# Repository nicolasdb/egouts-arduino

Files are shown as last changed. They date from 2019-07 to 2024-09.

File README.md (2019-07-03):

# MUSEE DES EGOUTS
Une maquette sur le cycle anthropique de l’eau et de supports didactiques  
Projet Arduino pour l'automatisation des écoulements d'eau.   

## Appel à projet remporté par:

**Ignacio Plaza De Giles** : architecte, maquettiste  
_Conception et réalisation + modelisation 3D, impression 3D, découpe laser_  
**Nicolas de Barquin** : co-fondateur de OpenFab  
_Conception et réalisation + support technique sur le design et l’électronique_  
**Juan Vandeput** : menuisier, ébéniste  
_Conception et réalisation + construction bois_  
**Alexandra Sebbag** : graphiste  
_Conception et réalisation des jeux + design et légendes de la maquette_  
**Hélène Mariage** : paysagiste, maquettiste  
_Conception et réalisation + communication, logistique_  

blob

## Storm simulation

arduino Board - LEDs orage



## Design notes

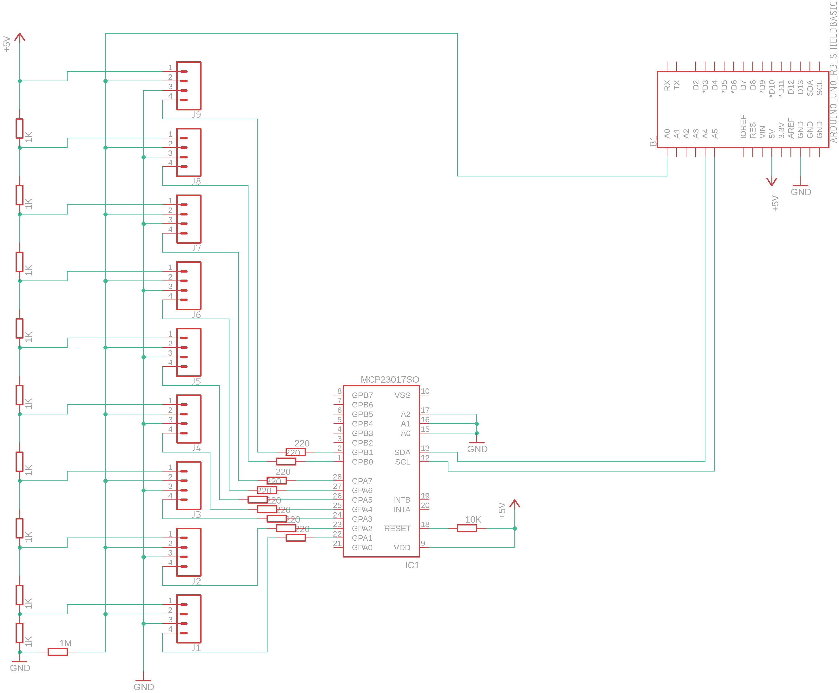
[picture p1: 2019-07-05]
ArduinoShield/schéma boutons.png

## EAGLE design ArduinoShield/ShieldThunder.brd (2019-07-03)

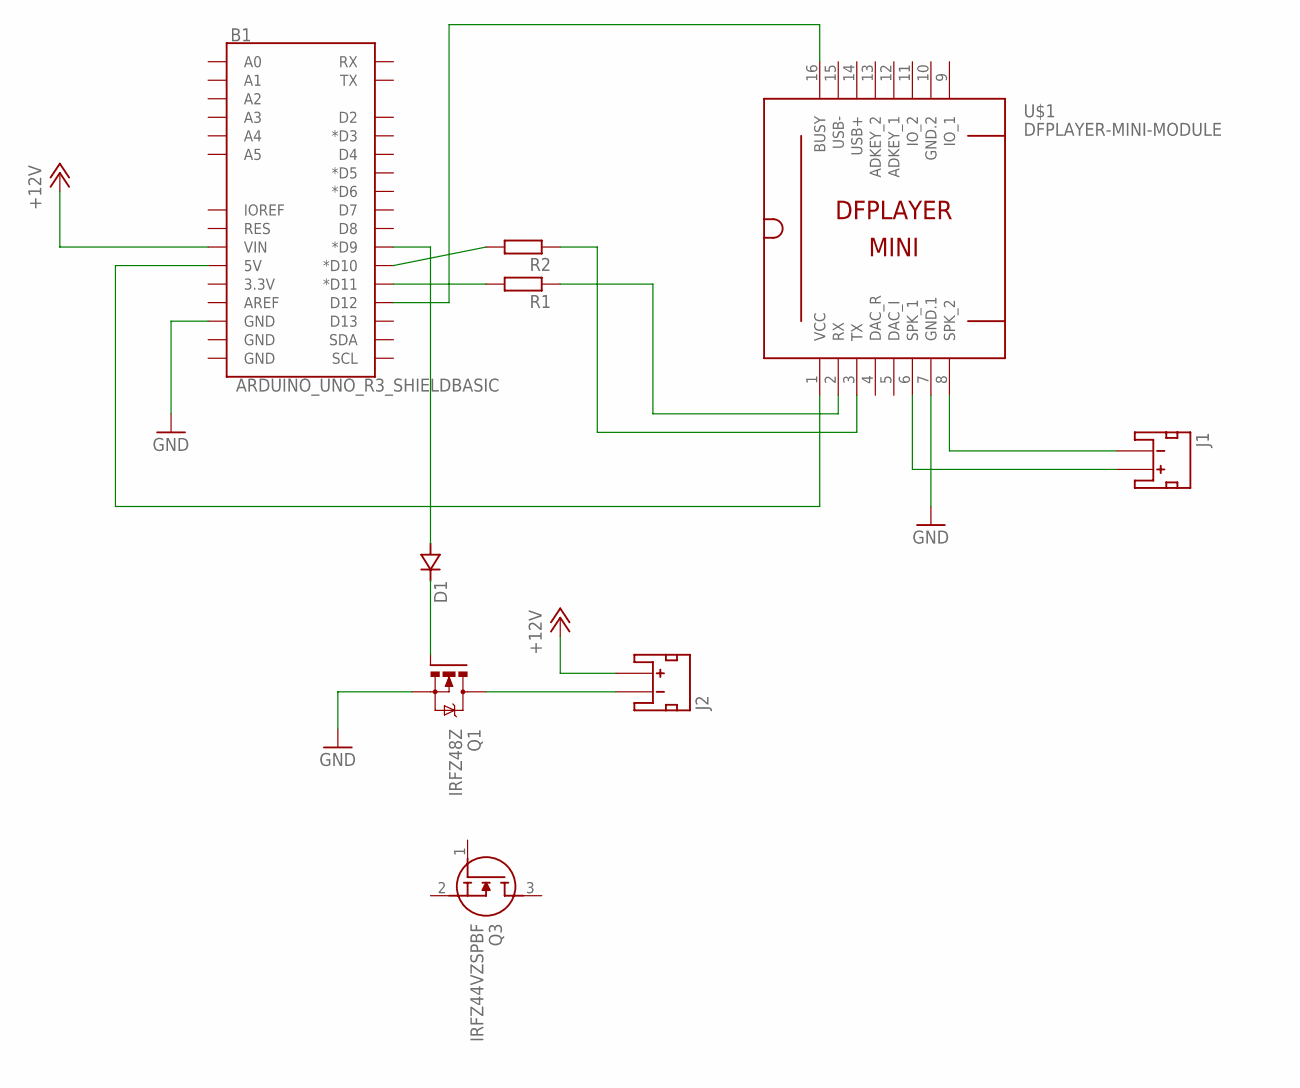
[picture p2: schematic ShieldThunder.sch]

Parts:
B1: ARDUINO_UNO_R3_SHIELDBASIC; UNO_R3_SHIELD
D1: DSOT23; SOT-23
J1, J2: JST_2MM_MALE; JST-2-SMD
Q1: IRFZ48Z; TO220BH
Q3: IRFZ44VZSPBF; D2PAK(TO-263AB)
R1, R2: R-EU_R0805; R0805
U$1: DFPLAYER-MINI-MODULE

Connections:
+12V: B1.VIN, J2.2 (+)
GND: B1.GND@2 (GND), Q1.S, U$1.7 (GND.1)
GND.2: U$1.10 (GND.2)
unnamed: B1.D10 (*D10), R2.2
unnamed: B1.D11 (*D11), R1.2
unnamed: R1.1, U$1.2 (RX)
unnamed: R2.1, U$1.3 (TX)
unnamed: B1.D12, U$1.16 (BUSY)
unnamed: J1.2 (+), U$1.6 (SPK_1)
unnamed: J1.1 (-), U$1.8 (SPK_2)
unnamed: B1.D9 (*D9), D1.3 (A)
unnamed: D1.1 (C), Q1.G
unnamed: J2.1 (-), Q1.D
unnamed: B1.5V, U$1.1 (VCC)

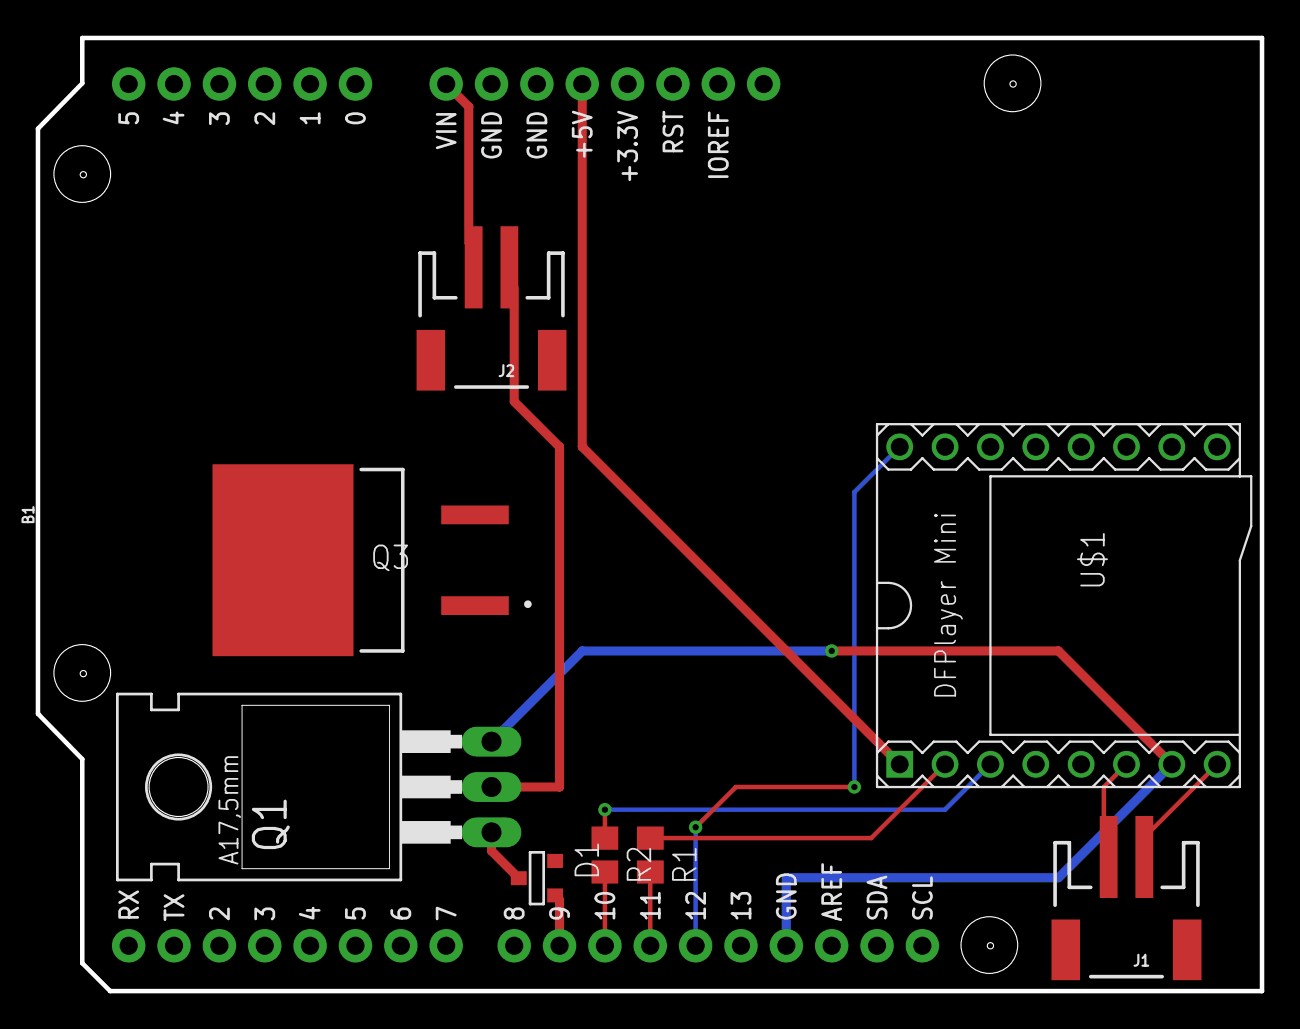
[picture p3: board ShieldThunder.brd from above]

Board: 2 copper layers, 68.5 x 53.4 mm, 9 parts (0 on the bottom side), 13 nets.

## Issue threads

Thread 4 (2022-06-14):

DFplayer mini setup

nicolasdb, 2022-06-14:
J'ai toujours des problèmes de son.
J'ai testé le module seul avec une activation par push button, ça fonctionne.
Et les bugs apparaissent avec la connexion à Arduino.
Je teste avec la proposition de [claudiusmarius](https://github.com/claudiusmarius)
https://github.com/claudiusmarius/Double-Player-Avec-ATtiny84

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

nicolasdb, 2022-06-14:
mes tests se font avec un petit HP 8ohm, mais l'installation finale est équipée de 2x 4ohm. ça a marché pendant 2 ans, sauf que ça ne marche pas à l'atelier sur un seul 4ohm similaire....

je vais tester d'en brancher 2

nicolasdb, 2022-06-14:
Problème aussi de surchauffe.
Le module chauffe rapidement, peut-être que l'ajout de la diode zener et les condo aidera.... à suivre.

nicolasdb, 2022-06-14:
Good,
les ajouts de Condensateurs et diode zener maintienne le module frais.
Mais j'ai encore eu des soucis de connection après la mise sous tension, un reset était nécessaire 1x.... que j'ai résolu pour l'instant en rajoutant un `delay(1000);` avant le chargement de la librairie mp3.
Juste de quoi laisser le temps au système de se stabiliser après mise sous tension. Peut-être les condensateurs.

J'ai encore un doute sur les HP.
celui de test en 8ohm fonctionne.

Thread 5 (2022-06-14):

détection série multiples Boutons d'arcade - instabilité

nicolasdb, 2022-06-14:
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

Le problème initial était le manque de PIN sur arduino, problème solutionné ensuite par l'ajout de multiplexer MCP23017.
Je pourrais renvoyer la détection INPUT des boutons sur le MCP0, mais je devrai alors revoir le code.
Ce qui n'est pas prévu dans cette révision.
J'ai 5 boutons poussoir monté en série, inspiré de ceci:

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
https://rayshobby.net/wordpress/multiple-button-inputs-using-arduino-analog-pin/

Mais j'observe une instabilité dans le système.
- Lorsque je branche l'alimentation, un bouton est automatiquement déclenché.
peut-être ajouter un condo, il doit y avoir une surtension qui acte comme un bouton... lequel?
- En fonction que j'alimente par transfo 9V, 12V sur l'arduino. Ou encore que j'ai l'USB connecté ou pas, lorsque je veux prendre mes mesures via le monitor,
la tension en sortie 5V est légèrement modifiée et ça fait varier la mesure sur le pin A0 (A3 dans mon code)
Et la mesure change au point que l'assignation des boutons changent. Les plages d'identification sont pourtant assez large...

```
for (;;) {

    if (etats == IDLE) {
      int buttonValue=analogRead(A3);
      Serial.print("Waiting entry");
      Serial.println(buttonValue);
      if (buttonValue>751) {                                         // read: 1013
        Serial.println("Button 1");
        buttonID = 1;
        etats = S1;
      } else if (buttonValue >= 726 && buttonValue < 925) {          // read: 815
        Serial.println("Button 2");
        buttonID = 2;
        // etats = IDLE;
        etats = S2;
      } else if (buttonValue >= 501 && buttonValue < 725) {          // read: 614
        Serial.println("Button 3");
        buttonID = 3;
        // etats = IDLE;
        etats = S3;
      } else if (buttonValue >= 251 && buttonValue < 500) {          // read: 409
        Serial.println("Button 4");
        buttonID = 4;
        // etats = IDLE;
        etats = S4;
      } else if (buttonValue >= 101 && buttonValue < 250) {          // read: 214
        Serial.println("Button 5");
        buttonID = 5;
        // etats = IDLE;
        etats = S5;
      }
    }
    vTaskDelay(1);
  }
```

nicolasdb, 2022-06-14:
ok, dans le cas précédent les R1K s'additionnaient. D'où peut-être trop d'instabilité dans les valeurs.

Je testerai selon cette proposition:
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

> We connect a single 100K resistor between GND and the analog input, with the analog input also connected to one leg of all of the push buttons. We then connect different resistors between the 5V and the second leg of each of the push buttons. It is important that each of these resistors are different values so that you get different voltages on the analog input, enabling you to identify each button.
https://www.the-diy-life.com/multiple-push-buttons-on-one-arduino-input/

nicolasdb, 2022-06-14:
Mise à jour:
- remplacement des résistances pour mode //
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
- et ajout d'un "debounce" software
```
void TaskButtons(void *pvParameters)
{
  (void) pvParameters;

  for (;;) {

    if (etats == IDLE) {
      int buttonValue=analogRead(A3);
      delay(20);
      int buttonValue2=analogRead(A3);
      Serial.print("Waiting entry");
      Serial.println(buttonValue);
      if (buttonValue >= 950 && buttonValue2 >= 950){                                      // 10R read: 1021
        Serial.println("Button 1");
        buttonID = 1;
        // etats = IDLE;
        etats = S1;
      } else if (buttonValue >= 876 && buttonValue < 949 && buttonValue2 >= 876 && buttonValue2 < 949) {          // 10K read: 930
        Serial.println("Button 2");
        buttonID = 2;
        // etats = IDLE;
        etats = S2;
      } else if (buttonValue >= 751 && buttonValue < 875 && buttonValue2 >= 751 && buttonValue2 < 875) {          // 22K read: 840
        Serial.println("Button 3");
        buttonID = 3;
        // etats = IDLE;
        etats = S3;
      } else if (buttonValue >= 351 && buttonValue < 750 && buttonValue2 >= 351 && buttonValue2 < 750) {          // 56K read: 659
        Serial.println("Button 4");
        buttonID = 4;
        // etats = IDLE;
        etats = S4;
      } else if (buttonValue >= 150 && buttonValue < 350 && buttonValue2 >= 150 && buttonValue2 < 350) {          // 210K read: 280
        Serial.println("Button 5");
        buttonID = 5;
        // etats = IDLE;
        etats = S5;
      }
    }
    vTaskDelay(1);
  }
}
```

ça à l'air pas mal.

Closed 2023-03-04.

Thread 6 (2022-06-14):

Activation des 16 relais

nicolasdb, 2022-06-14:
https://www.utmel.com/components/bc337-npn-transistor-pinout-datasheet-and-equivalents?id=347

nicolasdb, 2022-06-14:
J11 et J13 sont les pin 5V et GND que j'ai externalisé du header 10pin pour choisir entre une alimentation provenant de la carte controle ou via une alim externe sur les connecteurs en bas à droite du module.

nicolasdb, 2022-06-14:
Note pour une upgrade.
Est-ce que ULN2803 pourrait remplacer les transistors BC337

https://pijaeducation.com/arduino/relay/interfacing-of-relay-with-arduino-using-uln2003/

nicolasdb, 2022-06-18:
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

nicolasdb, 2022-06-18:
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

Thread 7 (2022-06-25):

Boite de simulation

nicolasdb, 2022-06-25:
En attendant que les PCB arrivent, je fabrique une boite de simulation pour tester la programmation sans la maquette.

à quoi sert le 3ème pin des connecteurs 5.5x2.1mm? (barrel power plugs)
https://electronics.stackexchange.com/questions/90529/what-to-do-with-third-contact-in-dc-barrel-plug-with-only-two-input-contacts

nicolasdb, 2022-06-25:
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

à quoi sert le 3ème pin des connecteurs 5.5x2.1mm? (barrel power plugs)
https://electronics.stackexchange.com/questions/90529/what-to-do-with-third-contact-in-dc-barrel-plug-with-only-two-input-contacts

nicolasdb, 2022-07-01:
Pour remplacer les 2 sorties leds-array en 12V, je place 2 leds 9V 402 de chez electron discount

https://www.befr.ebay.be/itm/140668935540

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

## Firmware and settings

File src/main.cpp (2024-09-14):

#include <Arduino.h>
#include <Arduino_FreeRTOS.h>         // Multitasking. Attention version 10.1.1-1!!
#include <SoftwareSerial.h>           // controle du module mp3
#include <DFRobotDFPlayerMini.h>      // controle du module mp3
#include <Wire.h>                     // controle des MCP
#include <Adafruit_MCP23X17.h>        // controle des MCP

#include <mp3.h>                      // controle storm du module mp3 - local

#define portCHAR char                 // resolve error: expected primary-expression before 'const'

// define tasks for Demo, AnalogRead buttons, set Actions, MP3 launch
void TaskDemo( void *pvParameters );          // define demo
TaskHandle_t xDemoHandle = NULL;              // nécessaire pour activer la pause et reprise de la tâche
void TaskButtons( void *pvParameters );       // define Buttons, pour l'écoute de quel bouton est activé
void TaskActions( void *pvParameters );       // define la tâche d'actions.
void TaskPump( void *pvParameters );

// define différent scénario = les actions déclenchées par les boutons lorsque pressé.
enum {
  IDLE,
  S1,S2,S3,S4,S5,S6,S7,S8
} etats;
int buttonID = 0;



// define MCP0 - registre pour les leds bouttons "scénario"
Adafruit_MCP23X17 mcp0;
// define MCP1 - registre pour les electrovannes via relais et options
Adafruit_MCP23X17 mcp1;

int ledButtonArray[] = {7,6,9,8,11,10,5,4};   // liste les pin utilisées sur mcp0 et leur ordre
int count = 0;                                // compteur pour scanner led k2000
int speed = 20;                               // delay pour scanner led k2000



// define n° relay for valves on MCP0 | n°relai>>n°valve
int pump = 0;         //pompe 220V
int ledCiterne = 1;   //citerne 5V
int sterput = 2;     //valve 1-- sterput maison
int citerne = 3;      //valve 2 citerne
int tImper = 4;       //valve 3 pluie toiture G
int tPlant = 5;       //valve 4 pluie toiture D
int egout = 6;       //valve 5 egout champignon
int bOrage = 7;      //valve 6 bassin d'orage
int ledBO2 = 8;       //bassin d'orage bas 5V
int ledBO1 = 9;       //bassin d'orage haut 5V
int pChamp = 10;       //valve 7 pluie champ
int pJardin = 11;      //valve 8 pluie jardin
int collecteur = 12;  //valve 9  collecteur maison (oeuf)
int ruePlace = 13;     //valve 10 rue et place
int riviere = 14;     //valve 11 rivière
int simVille = 15 ;   //valve 12 Maison voisine dans oeuf

// mapping leds
int nappe = 8;          // nappe Phréatique 12V _ Out2
int egg = 7;            // collecteur oeuf 12V - Out1
int sdb1 = 6;
int toilette = 2;
int cuisine = 5;
int arrosage = 4;
int lavelinge = 1;
int cave = 3;

/*--------------------------------------------------*/
/*---------------------- setup ---------------------*/
/*--------------------------------------------------*/
// setup function runs once when you press reset or power the board

void setup() {
  mp3setup();    // initialize mp3setup
  // Serial.begin(115200);

  // INPUT sensors
  pinMode(A3, INPUT);     // input pin buttons scénario

  for (size_t i = 2; i < 9 ; i++){
    pinMode(i, OUTPUT);
    digitalWrite(i,LOW);
    delay(10);
  }
// digitalWrite(2,HIGH);

  // MCP0, define all buttons
  mcp0.begin_I2C(0);                               // use default address 0
  for (size_t i = 0; i < 8 ; i++){
    mcp0.pinMode(ledButtonArray[i], OUTPUT);
    delay(50);
  }

  mcp1.begin_I2C(1);                               // use default address 1
  for (int j = 0; j < 16 ; j++){
    mcp1.pinMode(j, OUTPUT);
    mcp1.digitalWrite(j, LOW);
    delay(50);
  }

  // Serial.println("j'ai finis");
  etats = IDLE;

  // and at last,
  // set up tasks to run independently and their priority.
  xTaskCreate(
    TaskDemo
    ,  (const portCHAR *)"Demo"       // A name just for humans
    ,  128                            // This stack size can be checked & adjusted
                                      // by reading the Stack Highwater
    ,  NULL
    ,  1                              // Priority, with 3 (configMAX_PRIORITIES - 1) being the highest, and 0 being the lowest.
    ,  &xDemoHandle );

  xTaskCreate(
    TaskButtons
    ,  (const portCHAR *)"Buttons"    // A name just for humans
    ,  128                            // This stack size can be checked & adjusted
                                      // by reading the Stack Highwater
    ,  NULL
    ,  3                              // Priority, with 3 (configMAX_PRIORITIES - 1) being the highest, and 0 being the lowest.
    ,  NULL );

  xTaskCreate(
    TaskActions
    ,  (const portCHAR *)"Actions"    // A name just for humans
    ,  128                            // This stack size can be checked & adjusted by reading the Stack Highwater
    ,  NULL
    ,  2                              // Priority, with 3 (configMAX_PRIORITIES - 1) being the highest, and 0 being the lowest.
    ,  NULL );

}

/*--------------------------------------------------*/
/*---------------------- loop ----------------------*/
/*--------------------------------------------------*/
// the loop function is not use here, instead we use FreeRTOS's tasks
void loop()
{
}

/*------------------------------------------------------*/
/*---------------------- functions ---------------------*/
/*------------------------------------------------------*/

// this function will suspend Demo and turn off all led buttons
void suspendDemo () {
  vTaskSuspend(xDemoHandle);
  for (size_t i = 0 ; i < 8 ; i++){
    mcp0.digitalWrite(ledButtonArray[i], LOW);
    vTaskDelay(1);
    }
}

/*--------------------------------------------------*/
/*---------------------- Tasks ---------------------*/
/*--------------------------------------------------*/

/*---------------------- demo ---------------------*/
void TaskDemo(void *pvParameters)  // This is a task.
{
  (void) pvParameters;
  for (;;) {    // on joue la démo en loop : effet scanner k2000
    for (count = 2; count < 6 ; count++){
      mcp0.digitalWrite(ledButtonArray[count], HIGH);
      vTaskDelay(speed / portTICK_PERIOD_MS);
      mcp0.digitalWrite(ledButtonArray[count+1], HIGH);
      vTaskDelay(speed / portTICK_PERIOD_MS);
      mcp0.digitalWrite(ledButtonArray[count], LOW);
      vTaskDelay((speed*5) / portTICK_PERIOD_MS);
    }
    // vTaskDelay( 500 / portTICK_PERIOD_MS ); // wait for one second
    for (count = 6 ; count > 2 ; count--){
      mcp0.digitalWrite(ledButtonArray[count], HIGH);
      vTaskDelay(speed / portTICK_PERIOD_MS);
      mcp0.digitalWrite(ledButtonArray[count-1], HIGH);
      vTaskDelay(speed / portTICK_PERIOD_MS);
      mcp0.digitalWrite(ledButtonArray[count], LOW);
      vTaskDelay((speed*5) / portTICK_PERIOD_MS);
    }
  }
}


/*---------------------- buttons ---------------------*/
void TaskButtons(void *pvParameters)
{
  (void) pvParameters;

  for (;;) {

    if (etats == IDLE) {
      int buttonValue=analogRead(A3);
      // Serial.print("Waiting entry");
      // Serial.println(buttonValue);
      if (buttonValue>810) {
        // Serial.println("Button 8");
        buttonID = ledButtonArray[8-1];
        etats = IDLE;
      } else if (buttonValue > 700 && buttonValue < 809) {
        // Serial.println("Button 7");
        buttonID = ledButtonArray[7-1];
        etats = S5;
      } else if (buttonValue > 610 && buttonValue < 699) {
        // Serial.println("Button 6");
        buttonID = ledButtonArray[6-1];
        etats = S4;
      } else if (buttonValue > 500 && buttonValue < 609) {
        // Serial.println("Button 5");
        buttonID = ledButtonArray[5-1];
        etats = S3;
      } else if (buttonValue > 370 && buttonValue < 499) {
        // Serial.println("Button 4");
        buttonID = ledButtonArray[4-1];
        etats = S2;
      } else if (buttonValue > 270 && buttonValue < 369) {
        // Serial.println("Button 3");
        buttonID = ledButtonArray[3-1];
        etats = S1;
      } else if (buttonValue > 190 && buttonValue <269) {
        // Serial.println("Button 2");
        buttonID = ledButtonArray[2-1];
        etats = IDLE;
      } else if (buttonValue > 90 && buttonValue < 189) {
        // Serial.println("Button 1");
        buttonID = ledButtonArray[1-1];
        etats = IDLE;
      }
    }
    vTaskDelay(1);
  }
}

/*---------------------- actions ---------------------*/
void TaskActions(void *pvParameters)  // This is a task.
{
  for(;;) {
    switch (etats)
    {
    case IDLE:
      buttonID = 0;
      etats = IDLE;
      vTaskResume(xDemoHandle);
      break;


    case S1:              /*---------------------- case Pluie ---------------------*/
      suspendDemo();
      mcp0.digitalWrite(buttonID, HIGH);
        vTaskDelay( 1000 / portTICK_PERIOD_MS );    // wait for 1/2 second
// start scénario
      // eau de pluie, alimentation de la nappe Phréatique
      mcp1.digitalWrite(pump, HIGH);      // start pompe
        piste4(); // activation audio pluie 24'

      mcp1.digitalWrite(pChamp, HIGH);    // start pluie sur
      mcp1.digitalWrite(pJardin, HIGH);   // les surfaces perméables
        vTaskDelay( (1000 / portTICK_PERIOD_MS) * 15 );
      // Waiting x second
      digitalWrite(nappe, HIGH);          // turn on led nappe Phréatique
        vTaskDelay( (1000 / portTICK_PERIOD_MS) * 10 );
      mcp1.digitalWrite(pChamp, LOW);     // stop pluie
      mcp1.digitalWrite(pJardin, LOW);
      mcp1.digitalWrite(pump, LOW);       // stop pompe
        vTaskDelay( (1000 / portTICK_PERIOD_MS) * 3 );
      // on attend un peu pour l'histoire de la nappe Phréatique
      digitalWrite(nappe, LOW);           // turn off led nappe
        vTaskDelay( (1000 / portTICK_PERIOD_MS) * 1 );

// end scénario
      mcp0.digitalWrite(buttonID, LOW);
      etats = IDLE;
      break;

    case S2:              /*---------------------- case Eau potable ---------------------*/
      suspendDemo();
      mcp0.digitalWrite(buttonID, HIGH);
        vTaskDelay( 1000 / portTICK_PERIOD_MS ); // wait for 1/2 second
// start scénario
        // captation eau potable
        digitalWrite(nappe, HIGH);      // turn on nappe Phréatique
          vTaskDelay( (1000 / portTICK_PERIOD_MS) * 10 );
        // on pompe dans la nappe, ou dans la rivière
        digitalWrite(nappe, LOW);
          vTaskDelay( (1000 / portTICK_PERIOD_MS) * 1 );
          // Waiting pompage, chateau d'eau
        digitalWrite(cuisine, HIGH);  // turn on led cuisine
        piste3(); // piste audio robinet 20'
          vTaskDelay( (1000 / portTICK_PERIOD_MS) * 2 );
        //waiting vaisselle, ambiance cuisine
        // turn on pompe et activation du sterput, + led Cave.
        mcp1.digitalWrite(pump, HIGH);
          vTaskDelay( (1000 / portTICK_PERIOD_MS) * .5 );
        // waiting action robinet en cuisine
        // puis turn on sterput à la cave + led
        mcp1.digitalWrite(sterput, HIGH);
        digitalWrite(cave, HIGH);
          vTaskDelay( (1000 / portTICK_PERIOD_MS) * 3 );
        // Waiting trajet de l'eau jusqu'au collecteur rue
        mcp1.digitalWrite(collecteur, HIGH);
        digitalWrite(egg, HIGH);
          vTaskDelay( (1000 / portTICK_PERIOD_MS) * 10 );
          // Waiting end audio robinet
        digitalWrite(cuisine, LOW); // turn of led cuisine
          // Waiting et turn off sertup et led cave
          vTaskDelay( (1000 / portTICK_PERIOD_MS) * 2 );
        mcp1.digitalWrite(sterput, LOW);
        digitalWrite(cave, LOW);
          vTaskDelay( (1000 / portTICK_PERIOD_MS) * 2 );
        mcp1.digitalWrite(collecteur, LOW);
        digitalWrite(egg, LOW);
        mcp1.digitalWrite(pump, LOW);
          vTaskDelay( (1000 / portTICK_PERIOD_MS) * .5 );

// end scénario
      mcp0.digitalWrite(buttonID, LOW);
      // vTaskDelay( (1000 / portTICK_PERIOD_MS) * .5 );
      etats = IDLE;
    break;

    case S3:              /*---------------------- case Épuration ---------------------*/
      suspendDemo();
      mcp0.digitalWrite(buttonID, HIGH);
        vTaskDelay( 1000 / portTICK_PERIOD_MS ); // wait for 1/2 second
// start scénario

digitalWrite(sdb1, HIGH); // turn on sdb
piste5();  //piste audio douche 24'
  vTaskDelay( (1000 / portTICK_PERIOD_MS) * 5 );
  //wait douche, ajout des autres pièces d'eau.
mcp1.digitalWrite(pump, HIGH);  // turn on pompe
    vTaskDelay( (1000 / portTICK_PERIOD_MS) * .5 );
mcp1.digitalWrite(sterput, HIGH);
digitalWrite(cave, HIGH);
  // eau dans la chambre de visite
  vTaskDelay( (1000 / portTICK_PERIOD_MS) * 1 );
  digitalWrite(cuisine, HIGH);
digitalWrite(lavelinge, HIGH); // turn on lavelinge

  vTaskDelay( (1000 / portTICK_PERIOD_MS) * 4 );

  //waiting fin des actions maisons
  vTaskDelay( (1000 / portTICK_PERIOD_MS) * 2 );
  //waiting, l'eau arrive au collecteur rue (egg)
mcp1.digitalWrite(collecteur, HIGH);   //collecteur oeuf + led
digitalWrite(egg, HIGH);
digitalWrite(sdb1, LOW);
  vTaskDelay( (1000 / portTICK_PERIOD_MS) * 1 );
digitalWrite(lavelinge, LOW);
digitalWrite(cuisine, LOW);
  vTaskDelay( (1000 / portTICK_PERIOD_MS) * 2 );
  mcp1.digitalWrite(sterput, LOW);
  digitalWrite(cave, LOW);
mcp1.digitalWrite(bOrage, HIGH);  // l'eau monte un peu
  vTaskDelay( (1000 / portTICK_PERIOD_MS) * 2 );
  //waiting, l'eau arrive au champignon
mcp1.digitalWrite(bOrage, LOW);  // on arrête l'eau au bassin
  vTaskDelay( (1000 / portTICK_PERIOD_MS) * 15 );
  //waiting, l'eau transit jusqu'à la station d'épuration.
mcp1.digitalWrite(riviere, HIGH);
  vTaskDelay( (1000 / portTICK_PERIOD_MS) * 15 );
  mcp1.digitalWrite(collecteur, LOW);   //collecteur oeuf + led
  digitalWrite(egg, LOW);
  //waiting, eau à la rivière
mcp1.digitalWrite(riviere, LOW);
mcp1.digitalWrite(pump, LOW);

// end scénario
      mcp0.digitalWrite(buttonID, LOW);
      etats = IDLE;
    break;

    case S4:              /*---------------------- case Orage ---------------------*/
      suspendDemo();
      mcp0.digitalWrite(buttonID, HIGH);
        vTaskDelay( 1000 / portTICK_PERIOD_MS ); // wait for 1/2 second
// start scénario
        storm(1); // start Orage
        piste4(); // start audio pluie 24'
        mcp1.digitalWrite(pump, HIGH);  // turn on pompe
            vTaskDelay( (1000 / portTICK_PERIOD_MS) * .5 );
        mcp1.digitalWrite(tImper, HIGH);      // pluie toitures maison
        mcp1.digitalWrite(tPlant, HIGH);
        mcp1.digitalWrite(pJardin, HIGH);
        mcp1.digitalWrite(pChamp, HIGH);
          vTaskDelay( (1000 / portTICK_PERIOD_MS) * 10 );
          // Waiting, il pleut
        mcp1.digitalWrite(ruePlace, HIGH);    // eau sur rue&place
          vTaskDelay( (1000 / portTICK_PERIOD_MS) * 5 );
          // Waiting, l'eau coule sur la rue et la place
        mcp1.digitalWrite(tImper, LOW);     // turn off pluie
        mcp1.digitalWrite(tPlant, LOW);
        mcp1.digitalWrite(pJardin, LOW);
        mcp1.digitalWrite(pChamp, LOW);
          vTaskDelay( (1000 / portTICK_PERIOD_MS) * 1 );
          // Waiting, la pluie s'arrête mais l'eau arrive dans le collecteur
        mcp1.digitalWrite(collecteur, HIGH);   //collecteur oeuf + led
        digitalWrite(egg, HIGH);
          vTaskDelay( (1000 / portTICK_PERIOD_MS) * 3 );
          // l'eau s'est écoulée des ruePlace
        mcp1.digitalWrite(ruePlace, LOW);   // turn off rue&place
          vTaskDelay( (1000 / portTICK_PERIOD_MS) * .5 );
          // waiting, l'eau est dans le champignon, bOrage + led Haut + egout
        mcp1.digitalWrite(bOrage, HIGH);  // démo trop plein vers BassinOrage
        mcp1.digitalWrite(ledBO1, HIGH);
        mcp1.digitalWrite(egout, HIGH);   // l'eau s'écoule dans le champignon
          vTaskDelay( (1000 / portTICK_PERIOD_MS) * 16 );
          // waiting, turn off egg, l'orage est fini
        mcp1.digitalWrite(collecteur, LOW);
        digitalWrite(egg, LOW);
          vTaskDelay( (1000 / portTICK_PERIOD_MS) * 10 );
          //le trop plein s'est déversé dans le bassin, led bas + egout
        mcp1.digitalWrite(bOrage, LOW);
        mcp1.digitalWrite(ledBO1, LOW);
        mcp1.digitalWrite(ledBO2, HIGH);
          vTaskDelay( (1000 / portTICK_PERIOD_MS) * 10 );
          //waiting, vidange du BassinOrage
        mcp1.digitalWrite(ledBO2, LOW);
        mcp1.digitalWrite(egout, LOW);
          vTaskDelay( (1000 / portTICK_PERIOD_MS) * 1 );
        mcp1.digitalWrite(pump, LOW);
          vTaskDelay( (1000 / portTICK_PERIOD_MS) * .5 );

// end scénario
      mcp0.digitalWrite(buttonID, LOW);
      etats = IDLE;
    break;

    case S5:              /*---------------------- case Récup pluie ---------------------*/
      suspendDemo();
      mcp0.digitalWrite(buttonID, HIGH);
        vTaskDelay( 500 / portTICK_PERIOD_MS ); // wait for 1/2 second
// start scénario
        piste4(); // piste audio pluie 24'
        mcp1.digitalWrite(pump, HIGH);
          vTaskDelay( (1000 / portTICK_PERIOD_MS) * 1 );
          // il pleut sur les toitures
        mcp1.digitalWrite(tImper, HIGH);
        mcp1.digitalWrite(tPlant, HIGH);
          vTaskDelay( (1000 / portTICK_PERIOD_MS) * 5 );
        // Waiting, une captation de l'eau vers la citerne
        mcp1.digitalWrite(citerne, HIGH);
        mcp1.digitalWrite(ledCiterne, HIGH);
          vTaskDelay( (1000 / portTICK_PERIOD_MS) * 13 );
        // Waiting, la citerne se remplit.
        mcp1.digitalWrite(tImper, LOW);
        mcp1.digitalWrite(tPlant, LOW);
          vTaskDelay( (1000 / portTICK_PERIOD_MS) * 5 );
        // Waiting, la citerne continue de se remplir et s'arrête.
        mcp1.digitalWrite(citerne, LOW);
          vTaskDelay( (1000 / portTICK_PERIOD_MS) * 1 );

        piste1();  //piste audio lavelinge 26'
        // digitalWrite(lavelinge, HIGH);
        digitalWrite(arrosage, HIGH);
          vTaskDelay( (1000 / portTICK_PERIOD_MS) * 8 );
          //wait lavelinge, ajout de la pompe d'arrosage.
        // digitalWrite(lavelinge, LOW); // turn off lavelinge
        digitalWrite(toilette, HIGH);
          vTaskDelay( (1000 / portTICK_PERIOD_MS) * 3 );

        // piste2(); // piste audio toilette 10'
        mcp1.digitalWrite(collecteur, HIGH);
        vTaskDelay( (1000 / portTICK_PERIOD_MS) * .5 );
        digitalWrite(cave, HIGH);
        digitalWrite(egg, HIGH);
          vTaskDelay( (1000 / portTICK_PERIOD_MS) * 10 );
          vTaskDelay( (1000 / portTICK_PERIOD_MS) * 3 );
        // la pompe d'arrosage est éteinte
        digitalWrite(toilette, LOW);
        digitalWrite(arrosage, LOW);
          vTaskDelay( (1000 / portTICK_PERIOD_MS) * 2 );
          mcp1.digitalWrite(collecteur, LOW);
          mcp1.digitalWrite(pump, LOW);
          vTaskDelay( (1000 / portTICK_PERIOD_MS) * .5 );
          digitalWrite(cave, LOW);
          digitalWrite(egg, LOW);
          // waiting a bit pour la citerne
        mcp1.digitalWrite(ledCiterne, LOW);

// end scénario
      mcp0.digitalWrite(buttonID, LOW);
      // vTaskDelay( (1000 / portTICK_PERIOD_MS) * .5 );
      etats = IDLE;
    break;
    case S6:
      suspendDemo();
      mcp0.digitalWrite(buttonID, HIGH);
      vTaskDelay( 1000 / portTICK_PERIOD_MS ); // wait for one second
      mcp0.digitalWrite(buttonID, LOW);
      etats = IDLE;
      break;
    case S7:
      suspendDemo();
      mcp0.digitalWrite(buttonID, HIGH);
      vTaskDelay( 1000 / portTICK_PERIOD_MS ); // wait for one second
      mcp0.digitalWrite(buttonID, LOW);
      etats = IDLE;
      break;
    case S8:
      suspendDemo();
      mcp0.digitalWrite(buttonID, HIGH);
      vTaskDelay( 1000 / portTICK_PERIOD_MS ); // wait for one second
      mcp0.digitalWrite(buttonID, LOW);
      etats = IDLE;
      break;



    }
    vTaskDelay(1);
  }
}

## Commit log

2019-06-21 add fade and start on mp3
    fade = juste un blink commun des pins 345
    le vrai fade viendra plus tard.
2019-06-21 bug in mp3
    error: '*****' was not declared in this scope
    a lot
    [main.cpp]
2019-06-24 it's working
    with just 3 buttons and thunder mp3
2019-06-25 yeah ça remarche
    Idle ok,
    Boutons ok.
    LedsBoutons ok,
    mp3 ok,
2019-06-26 update 9 scenarios
    + init EagleBoard
    [Shield00.sch, ShieldThunder.brd, ShieldThunder.sch]
2019-07-05 fine tune sur schem and delays
    getting down to 7 buttons,
    I set a 8th on hardware, just in case
2019-07-05 add mp3, mcp1 et 2 and pumplevel
    [Shield00.sch]
2019-07-05 end v1 schemboard
    [Shield00.sch]
2019-07-05 fail, pump task
    the rest is ok, sort of.
    [main.cpp]
2019-07-06 pump still not working
    [Shield00.sch]
2019-07-08 passage sur shield
    que les boutons.
    Réordonne les num et leds boutons
2019-07-09 add relais 0-16
    [Shield00.sch]
2019-07-11 add arduino on shield
    and some stuffs
2019-07-12 delete mcp2, add leds controls
    assez de pins sur arduino pour les quelques leds qui restent à controler.
    [Shield00.sch]
2019-07-12 last leds control, shield completed
    Version1, hopeSO
    [Shield00.sch]
2019-08-21 cleaning and update for test IRL
    still no pump action
2019-08-22 update list valves
2019-08-23 ajout pistes sons et prepa valves
2019-08-28 change to 2N4401 and connection to VSS
    [Shield00.sch]
2019-08-30 mise à jour des valves
2019-09-03 last test, still a bug with IDLE LEDs
    [main.cpp]
2019-09-12 correction suite à la remise
    [Shield00.sch]
2020-06-16 update timing scénario
    attention à la mise à jour freeRTOS qui fait buger la syntaxe. use FreeRTOS 10.1.1-1
    [main.cpp]
2022-05-23 no change, but new error from freeRTOS solved
    [main.cpp]
2024-09-14 Adjustment to new set of valves

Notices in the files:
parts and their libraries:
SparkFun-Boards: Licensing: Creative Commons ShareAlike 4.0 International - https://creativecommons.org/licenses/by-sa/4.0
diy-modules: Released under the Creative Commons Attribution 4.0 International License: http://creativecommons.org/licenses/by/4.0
